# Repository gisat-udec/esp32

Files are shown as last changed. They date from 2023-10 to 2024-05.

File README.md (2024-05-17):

# ESP32

Mini resumen de su vida

## Cansat

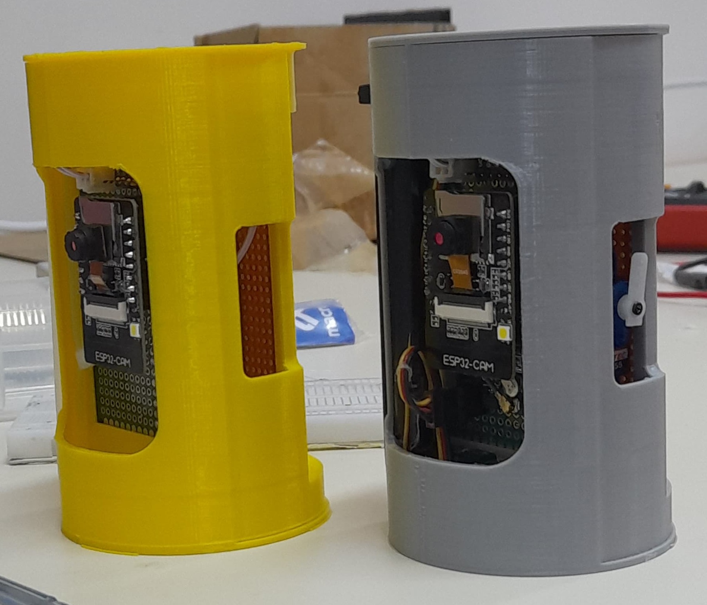
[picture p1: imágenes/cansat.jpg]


### Componentes

#### Microcontrolador principal

Ai-Thinker ESP32-CAM

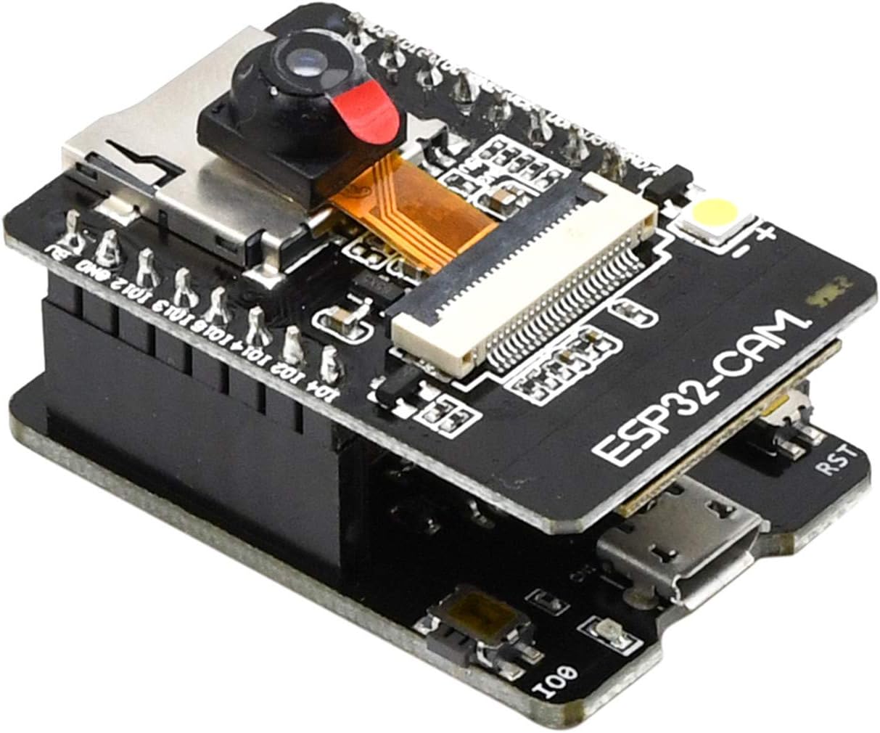
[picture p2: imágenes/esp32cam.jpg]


Copia de aliexpress de la version Ai-Thinker, incluye una cámara y ranura para tarjeta SD, utiles para la grabación y registro de datos en vuelo.

#### Sensores

##### BME680

Ofrece lecturas de temperatura, presión y humedad. Conectado por I2C y programado con la libreria de BOSCH.

##### BNO080

Sistema integrado de acelerómetro, magnetómetro y giroscopio. Realiza su propia fusión de sensores para entregar un cuaternión de orientación y aceleración lineal con o sin gravedad.

##### ATGM336H

GPS pequeño conectado por serial.

##### Lilygo T-BAT

Módulo de energía con ranura para una batería 18650.

#### Actuador

##### Servo SG90

Conectado a un elástico que sostiene una tapa lateral para que al soltarlo se despliegue un paracaídas. Por falta de tiempo no se alcanzó a implementar.

## Estación en tierra

### Componentes

#### Microcontrolador principal

Lilygo T-Internet-COM

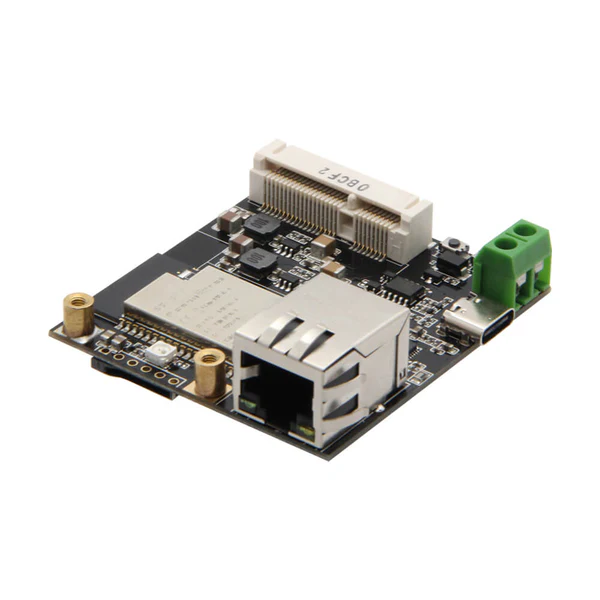
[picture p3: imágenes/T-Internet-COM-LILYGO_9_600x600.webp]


Vendido por el mismo fabricante en Aliexpress. Basado en el ESP32 básico recibe la información y la retransmite por el puerto Ethernet a un computador. Esto porque la conexión serial es demasiado lenta para la cantidad de datos que se reciben por wifi.

## FIDAE

El Cansat fue expuesto en la FIDAE 2024 como relleno para el stand, a pesar de lo crudo que estaba en desarrollo (se terminó de programar la demo en la mañana del segundo día de exposición) la gente demostró interés y generó discusión sobre el trabajo con estas tecnologías en universidades o colegios.

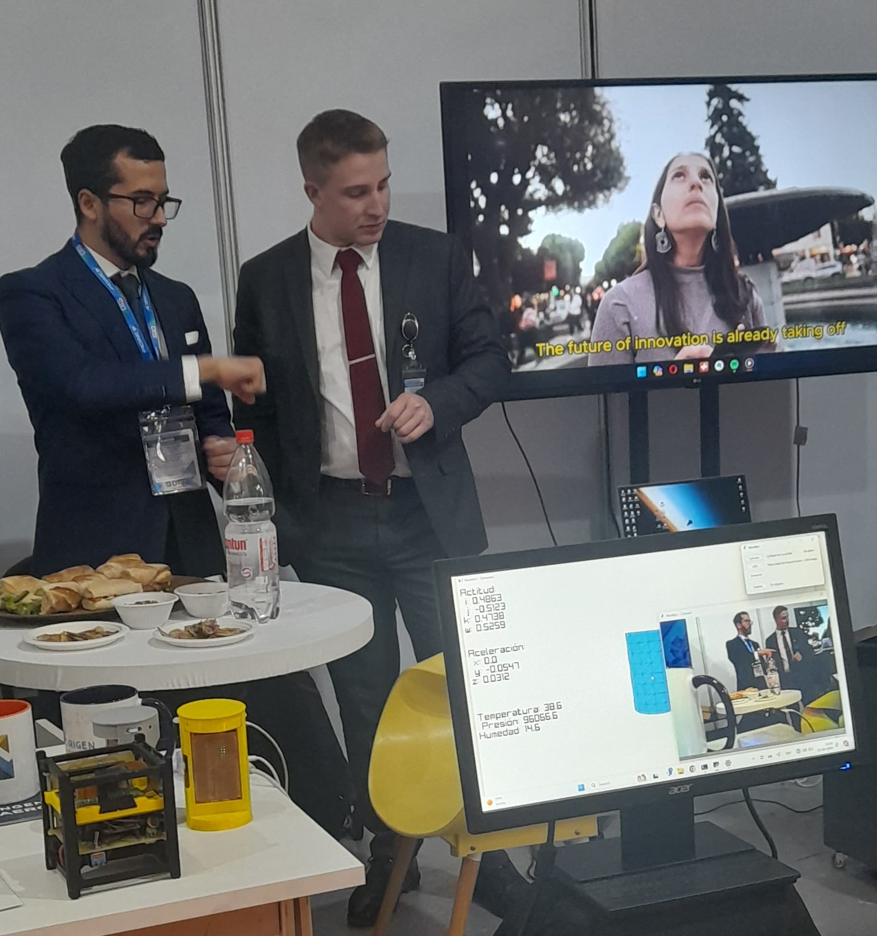
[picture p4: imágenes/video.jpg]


### Resultados

La conexión por wifi con paquetes en modo "promiscuo" fue exitosa, un avance que se aprendio con el Cansat anterior que tambien funcionaba de la misma manera. En FIDAE había **mucha** intereferencia en la banda de 2.4GHz y una conexión normal hubiese fallado.

En la demo se presentaba un modelo 3D del Cansat que reflejaba la orientación entregada por el sensor de actitud, se imprimían lecturas de aceleración y condiciones ambientales además de mostrar el video en vivo. Esta demostración logró generar interés sobre que es lo que se está haciendo en la universidad.

El trabajo con microcontroladores ESP32 es también significativo porque estos se están utilizando mucho para este tipo de proyectos (con globos aerostáticos). En comparación con Arduino tienen el mismo costo, son solo un poco más difíciles de programar y ofrecen órdenes de magnitud mayor capacidad de procesamiento y por lo tanto aplicaciones que se les puede dar. El video en vivo es un ejemplo.

### Problemas a tratar en la siguiente iteración

#### Falta de pines en el ESP32-CAM

El ESP32-CAM tiene muy pocos pines disponibles para utilizar. Si se activa la cámara y la interfaz con tarjeta SD solo queda libre un par de pines para la comunicación I2C y nada más. Se intentó conectar el servo, pero siempre ocurría una interferencia en las líneas con otro componente que ya la estuviese ocupando.

#### Baja confiabilidad de enlace

Si bien en FIDAE se logro conectar, el enlace funcionaba solo si estaban a hasta 10 centímetros de distancia la estación en tierra con el CANSAT, más alla y se perdía toda la comunicación. Las causas son la interefencia presente en la feria pero también la implementación del modo promiscuo.

El modo promiscuo es la creación de paquetes wifi que siguen parte de la normativa IEEE 802.11 pero no completamente. En una aplicación normal ambos terminales wifi intercambian nombre de la red y contraseña y luego comienzan a transmitir información. En el modo promiscuo se salta esta parte y los terminales inundan el ambiente con paquetes de datos. El omitir el handshake de conexión reduce los tiempos de espera para reanudar una conexión en caso de perdida, pero no cumple con el estandar por lo que es algo a lo que los fabricantes no le dan mucho soporte, incluyendo Espressif. Al no tener soporte los intentos para solucionar problemas de conexión pasan a ser trabajo experimental lo cual se escapa un poco de lo que abarca el proyecto.

#### Implementación del paracaídas

Aun falta ver el diseño que tendrá la tapa y como estará conectado el elástico.

#### Interruptor

El módulo de energía utilizado no incluye una interfaz para un interruptor por lo que para apagar el Cansat se debe quitar la batería, algo más o menos difícil en el reducido espacio.

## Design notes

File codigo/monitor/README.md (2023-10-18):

# Monitor

Programa de estación en tierra con el propósito de monitorear y llevar un registro de vuelo local del satélite. La información es proporcionada por el microcontrolador en tierra que retransmite los datos recibidos al puerto Ethernet del computador.

### Funcionalidad

- [x] Decodificar mensajes recibidos del satélite
- [x] Mostrar estado de la conexión (RSSI, velocidad)
- [ ] Codificar y enviar mensajes al satélite
- [ ] Mostrar información de sensores
  - [ ] IMU
  - [ ] Ambiente
  - [ ] GPS
  - [x] Cámara
- [ ] Grabar información de sensores

### Ejecutar

#### Prerequisitos

1. [Windows Terminal](https://aka.ms/terminal)

2. [Python](https://www.python.org/downloads/windows/)

3. [Repositorio](https://github.com/gisat-udec/esp32/archive/refs/heads/main.zip)

#### Instrucciones

1. Descomprimir archivos del repositorio y dirigirse a la carpeta "monitor", con click derecho "Abrir en Terminal"

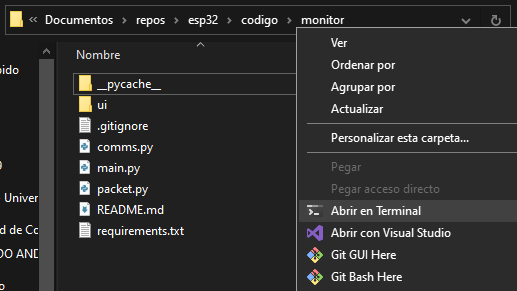
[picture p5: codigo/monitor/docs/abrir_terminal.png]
Abrir terminal


2. Instalar dependencias de Python con comando `pip install -r requirements.txt`

3. Ejecutar codigo con `python main.py`

### Librerías

El programa está escrito en Python 3 con las librerías [Tkinter](https://docs.python.org/3/library/tkinter.html) para generar la interfaz gráfica y [asyncio](https://docs.python.org/3/library/asyncio.html) para la comunicación con el microcontrolador en tierra de manera asincrónica, ver `requirements.txt` para revisar todas las dependencias.

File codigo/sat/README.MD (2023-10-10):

## Firmware satélite ESP-32

Sketch de Arduino creado para Arduino IDE 2.2.1

#### Placa

- AI Thinker ESP32-CAM

#### Dependencias

- [esp32](https://github.com/espressif/arduino-esp32)
- [BSEC Software Library](https://github.com/boschsensortec/BSEC-Arduino-library)
- [Sparkfun BNO080 Cortex Based IMU](https://github.com/sparkfun/SparkFun_BNO080_Arduino_Library)
- [TinyGPSPlus](https://github.com/mikalhart/TinyGPSPlus)

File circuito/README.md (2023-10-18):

## Diagrama de satélite

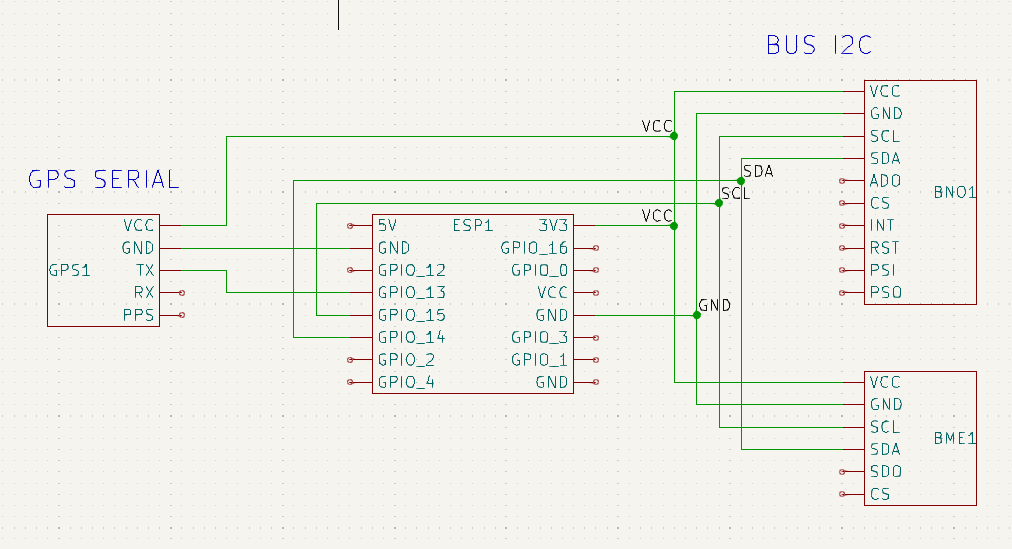
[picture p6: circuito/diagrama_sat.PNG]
Diagrama satélite


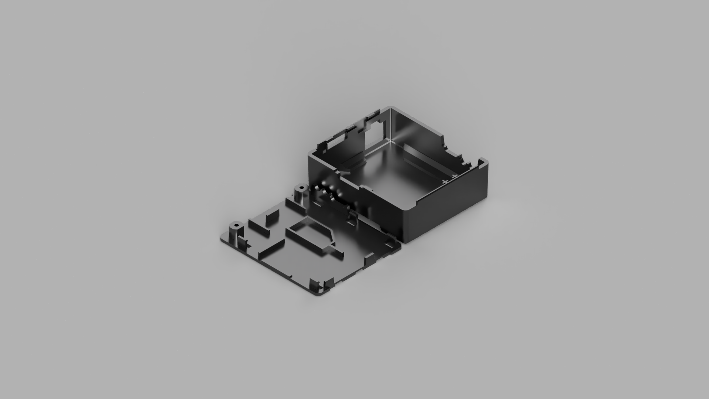
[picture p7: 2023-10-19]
modelos/gs/lilygov1.png

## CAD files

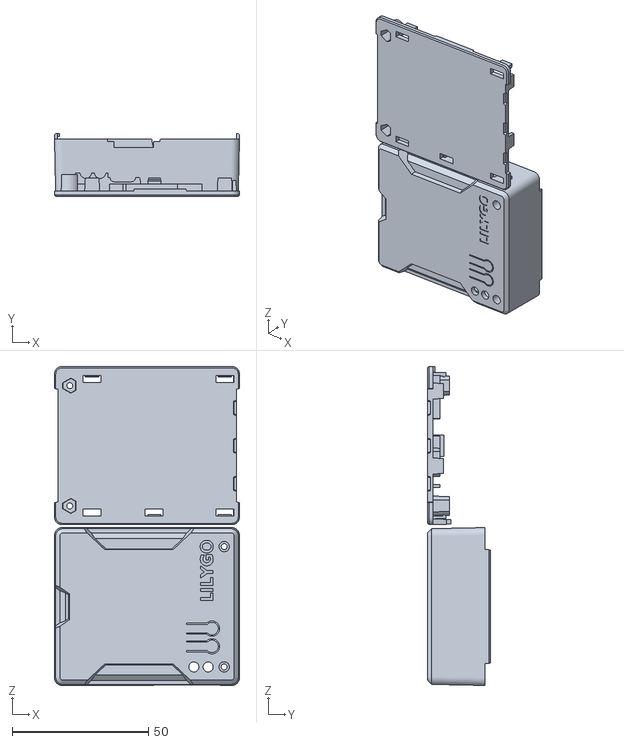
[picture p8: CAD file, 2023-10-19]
modelos/gs/lilygov1.stl
67.9 x 23.0 x 116.9

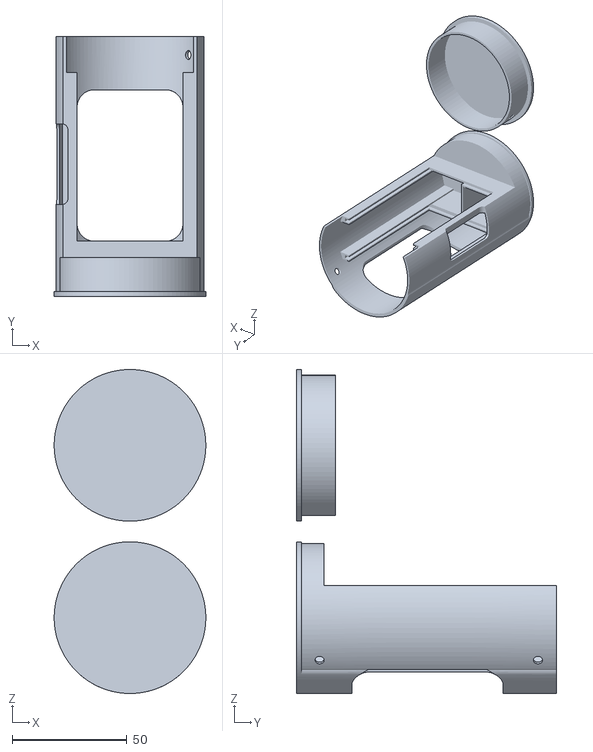
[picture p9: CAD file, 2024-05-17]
modelos/sat/CANSAT_vFIDAE.stl
66.0 x 113.0 x 141.0

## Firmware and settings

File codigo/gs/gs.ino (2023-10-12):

#include <Arduino.h>
#include <freertos/FreeRTOS.h>
#include <esp_event.h>
#include "src/wifi.hpp"
#include "src/ethernet.hpp"
#include "src/packet.hpp"

void setup() {
    Serial.begin(115200);
    ESP_ERROR_CHECK(esp_event_loop_create_default());
    wifi::init();
    eth::init();
    // timer regular para reportar conexión a python
    TimerHandle_t ping_timer = xTimerCreate("ping timer", pdMS_TO_TICKS(1000), pdTRUE, NULL,
        [](TimerHandle_t xTimer) {
            int time = millis();
            eth::send(Packet(PacketType::Ping, sizeof(time), &time));
        });
    xTimerStart(ping_timer, 0);
}

IRAM_ATTR void loop() {
    vTaskDelay(1000);
}

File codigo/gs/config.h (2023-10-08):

#pragma once

#define EMAC_CLK_MODE   EMAC_CLK_OUT
#define EMAC_CLK_GPIO   EMAC_APPL_CLK_OUT_GPIO
#define ETH_POWER_PIN   4
#define ETH_ADDR        0
#define ETH_MDC_PIN     23
#define ETH_MDIO_PIN    18

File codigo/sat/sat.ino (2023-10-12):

#include <Arduino.h>
#include <FreeRTOS/FreeRTOS.h>
#include <FreeRTOS/task.h>
#include <Wire.h>

#include "src/sensor/sensor.hpp"
#include "src/sensor/sensor_task.hpp"
#include "src/wifi.hpp"

#define LED_PIN GPIO_NUM_33

SensorTask *i2c_task;
SensorTask *camera_task;
SensorTask *gps_task;

void setup() {
    Serial.begin(115200);
    Wire.begin(14, 15);
    Wire.setClock(400000);

    i2c_task = new SensorTask("I2C", 6000);
    i2c_task->add(dynamic_cast<Sensor *>(new BNO080_c()));
    i2c_task->add(dynamic_cast<Sensor *>(new BME680_c()));
    i2c_task->run(1);

    camera_task = new SensorTask("CAMERA", 15000);
    camera_task->add(dynamic_cast<Sensor *>(new OV2640_c()));
    camera_task->run(1);

    gps_task = new SensorTask("GPS", 7000);
    gps_task->add(dynamic_cast<Sensor *>(new ATGM336H_c()));
    gps_task->run(0);

    delay(2);
    wifi::init();

    xTaskCreatePinnedToCore([](void *) -> void {
        gpio_set_direction(LED_PIN, GPIO_MODE_OUTPUT);
        TickType_t wake = xTaskGetTickCount();
        const TickType_t freq = pdMS_TO_TICKS(500);
        while (1) {
            gpio_set_level(LED_PIN, 0);
            vTaskDelay(pdMS_TO_TICKS(100));
            gpio_set_level(LED_PIN, 1);
            vTaskDelayUntil(&wake, freq);
        }
        }, "led flash", configMINIMAL_STACK_SIZE, NULL, 1, nullptr, 0);
}

std::vector<Packet> tosend;
void loop() {
    i2c_task->get(tosend);
    camera_task->get(tosend);
    gps_task->get(tosend);
    if (!tosend.empty()) {
        wifi::send(tosend);
        tosend.clear();
    }
}

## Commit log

2023-10-08 caleta de cosas
2023-10-10 add time to bme and gps, separate sensor task cores
2023-10-10 intento fallido de mostrar mapa
2023-10-10 sensor header
2023-10-10 flash led
2023-10-10 bosquejo de documentacion
2023-10-10 limitar framerate
2023-10-10 fix camara crashea en captura de arboles, fix timing de framerate despues de periodios de bajo framerate
    [camera.cpp, sat.ino]
2023-10-12 sensor source, remove framerate cap
2023-10-12 separar archivos ui de python
2023-10-18 instrucciones y print sensores
2023-10-18 arreglar tipos de imu
2023-10-18 nuevo link de windows terminal
2023-10-19 modelo estacion en tierra
    [lilygo v1.stl]
2023-10-19 renombrar archivos
    [lilygov1.stl]
2024-04-09 directorio de compilacion
